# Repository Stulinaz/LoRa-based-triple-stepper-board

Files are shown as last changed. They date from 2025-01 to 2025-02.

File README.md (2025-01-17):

<!-- For .md file development refers to https://docs.github.com/en -->
# LoRa Wireless Triple Stepper Controller 

## Build for 7th PCBWAy Project Design Contest

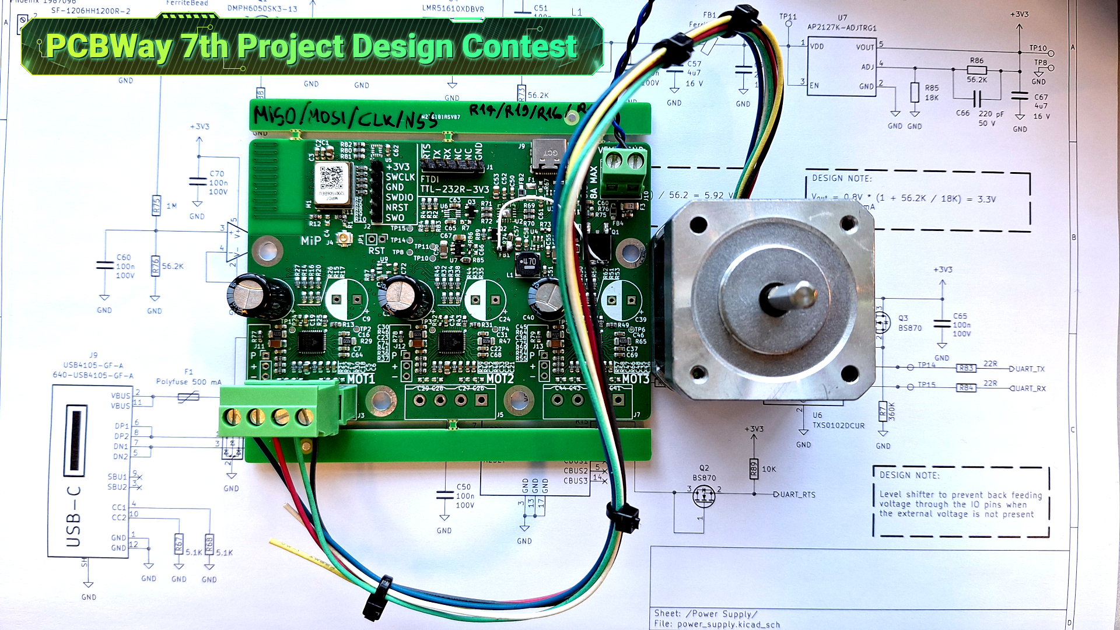
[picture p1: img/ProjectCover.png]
img_cover


[CLICK HERE](https://www.pcbway.com/project/shareproject/LoRa_based_triple_stepper_board_7cf3be2c.html) to see the project.

Designed to remote control up to three axis mechatronic system.
Build with [MIPOT](https://www.mipot.com) [32001506DEU](https://mipot.com/en/products/mip-series/dual-core/32001506deu/) LoRa Open Core module based on 
[STM32WL55JC](https://www.st.com/en/microcontrollers-microprocessors/stm32wl55cc.html) dual core microcontroller.

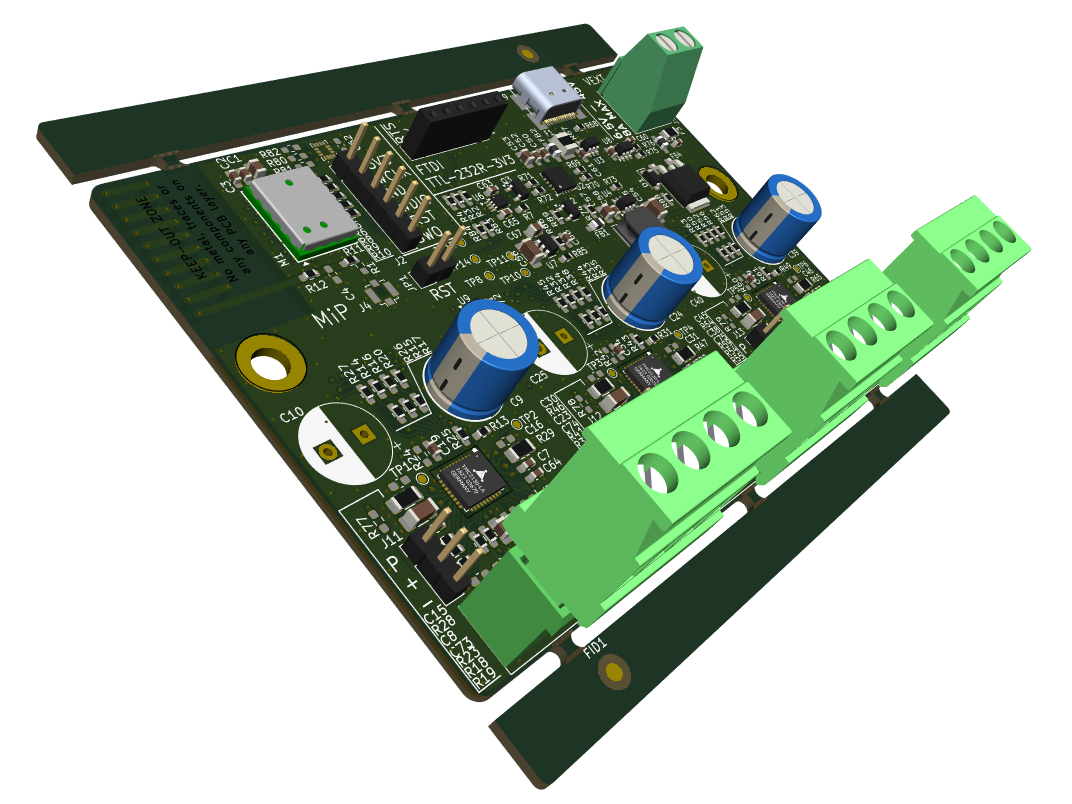
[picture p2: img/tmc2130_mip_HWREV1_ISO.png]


## Top Side of the board

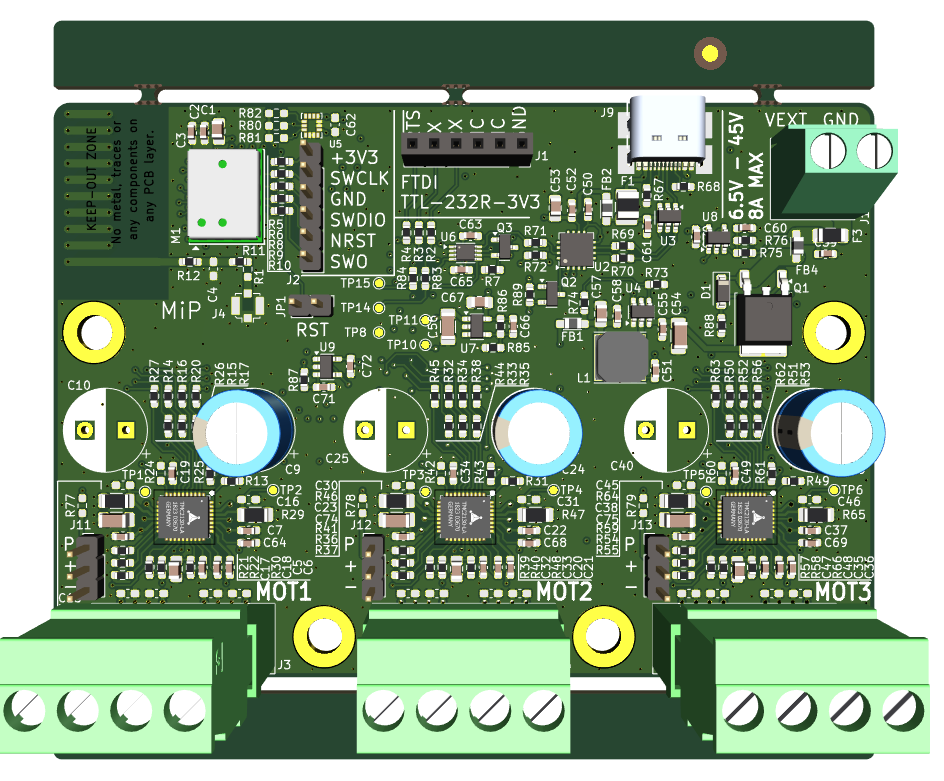
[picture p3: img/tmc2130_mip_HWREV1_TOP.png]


## Bottom Side of The board

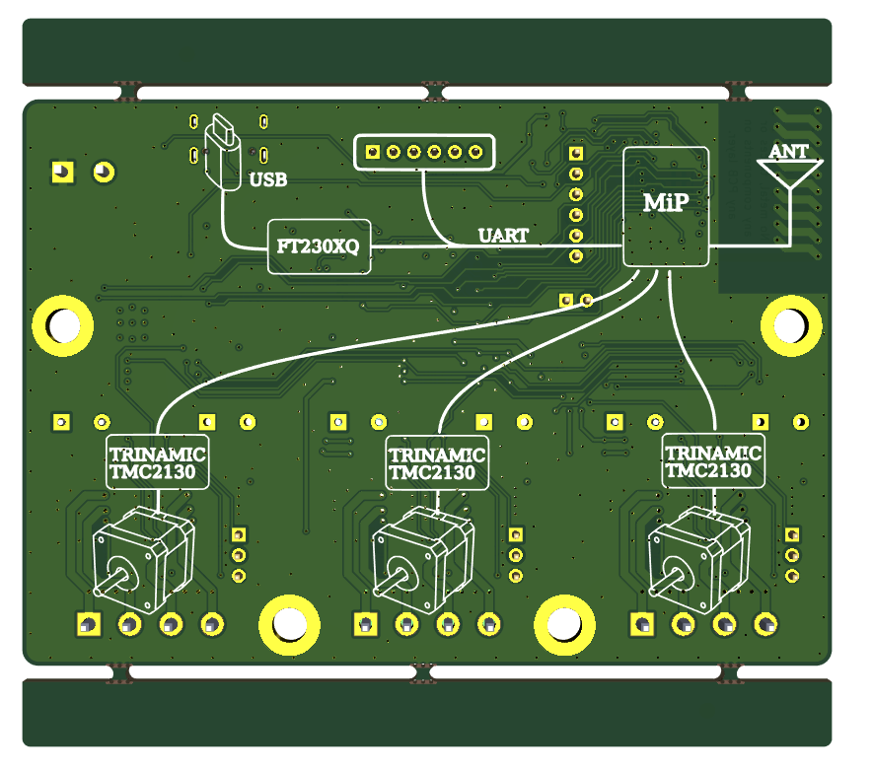
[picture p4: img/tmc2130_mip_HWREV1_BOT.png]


## Board with 4 layers for EMI Compliance

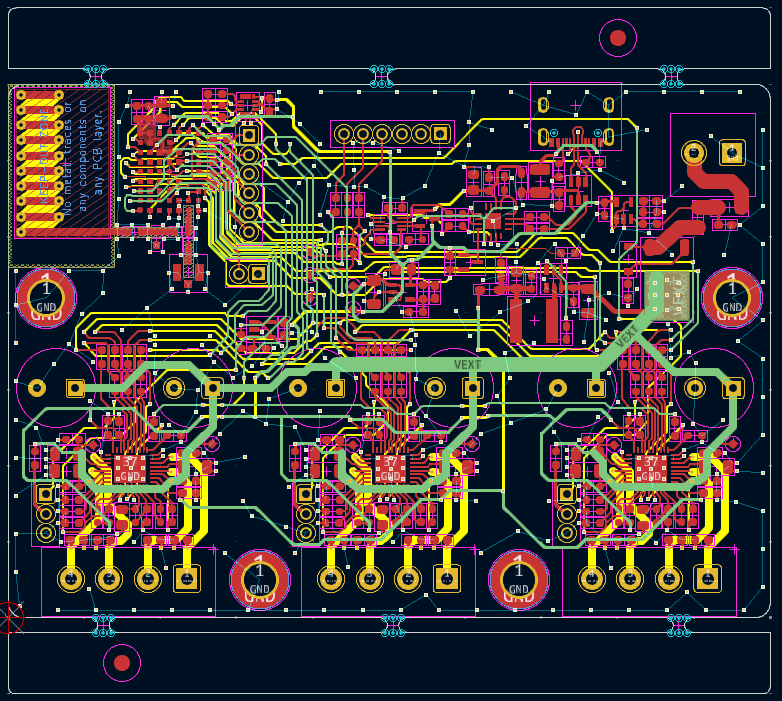
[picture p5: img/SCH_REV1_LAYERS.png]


## Build with Kicad

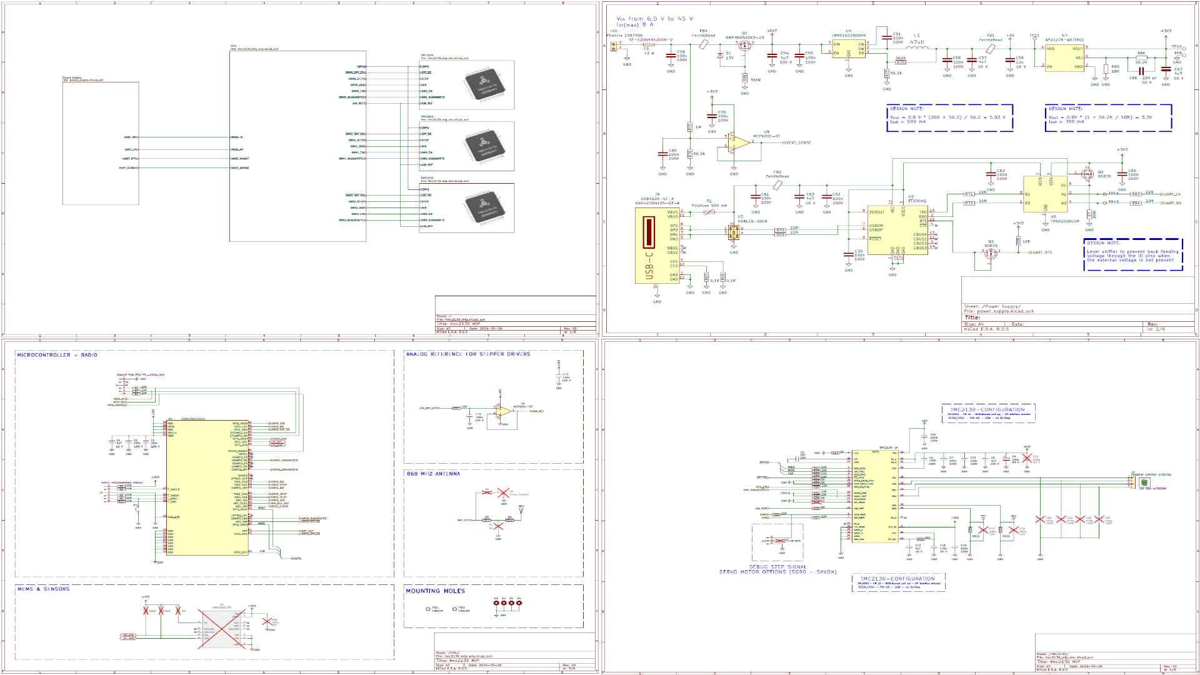
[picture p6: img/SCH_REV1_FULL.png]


## Main firwmare files for a quick view

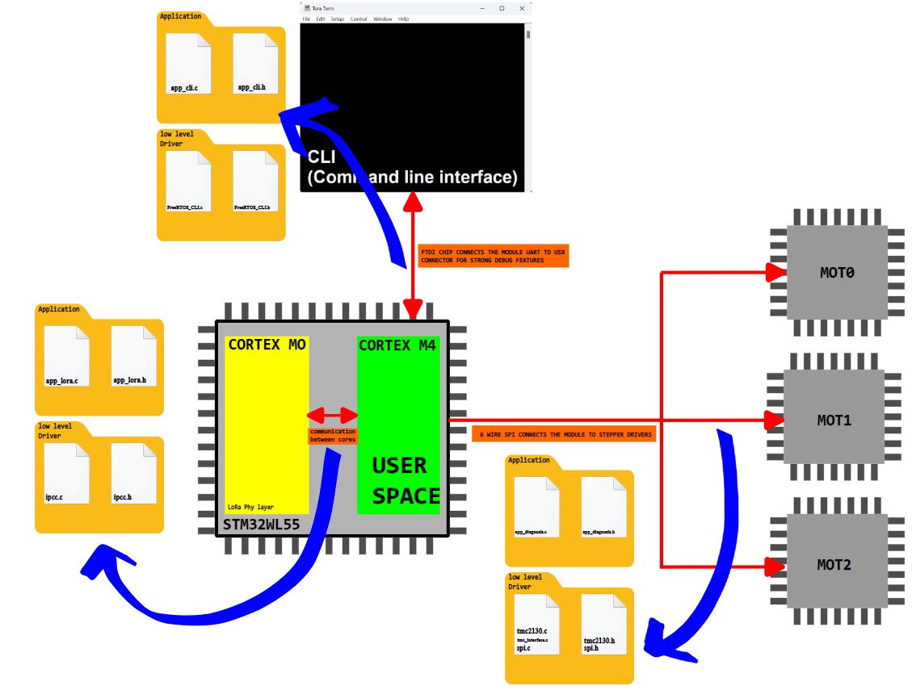
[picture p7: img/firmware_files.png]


## Pcb and stencil order on pcbway

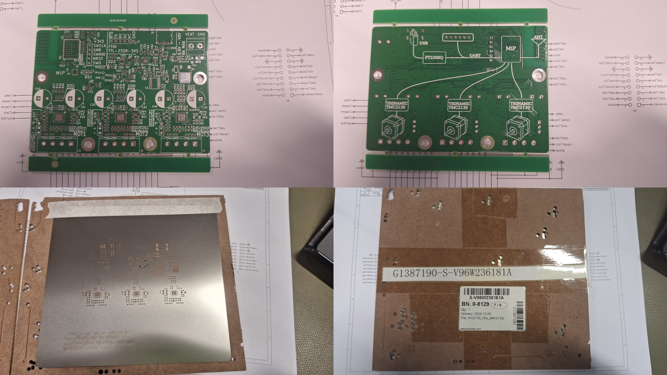
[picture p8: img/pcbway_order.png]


## Mode of Operation

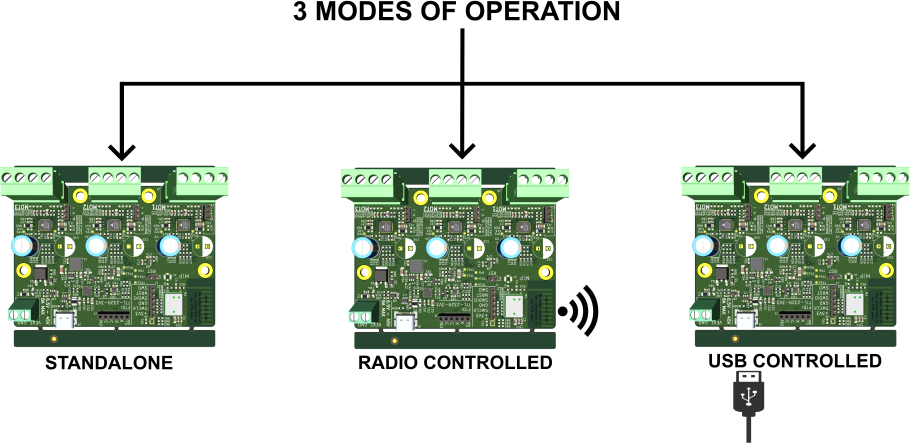
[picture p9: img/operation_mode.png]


## Closeup

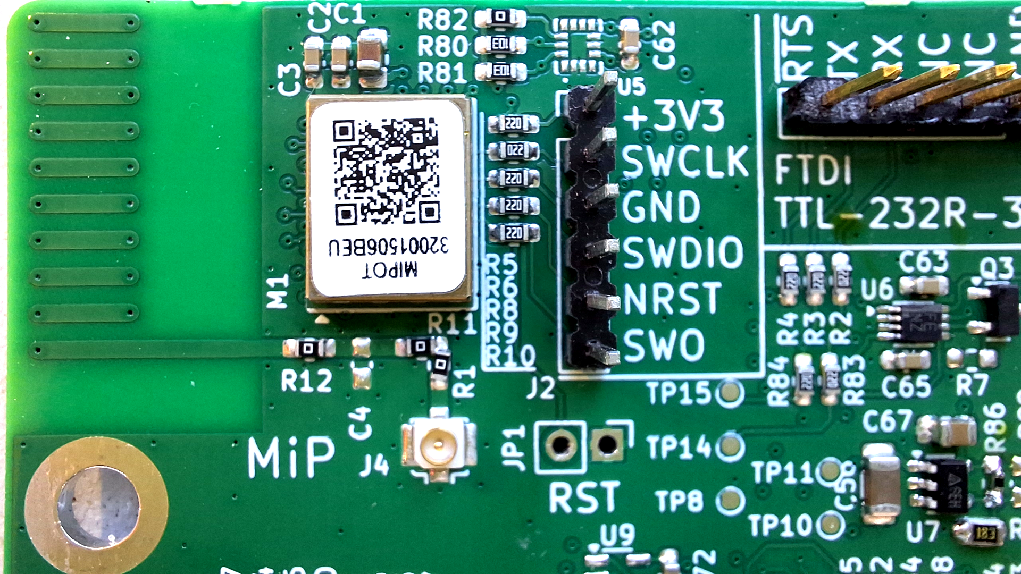
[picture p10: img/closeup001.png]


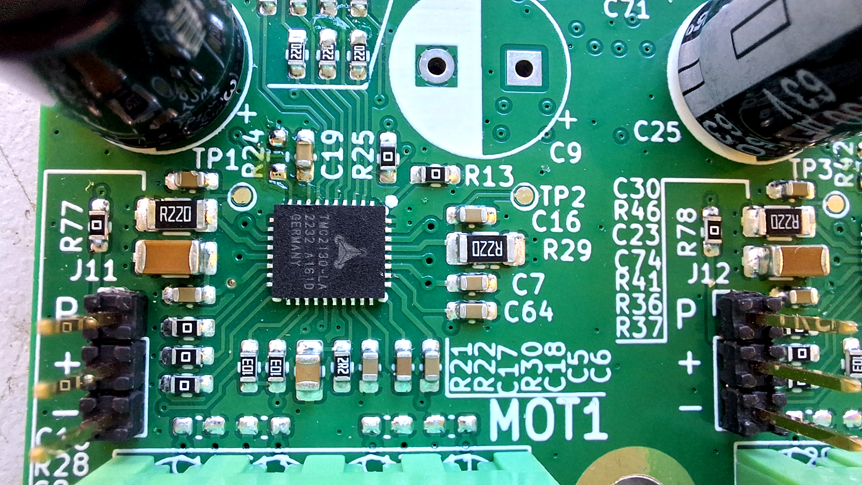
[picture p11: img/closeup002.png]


## SPI commonucation between microcontroller and TMC2130 Drivers

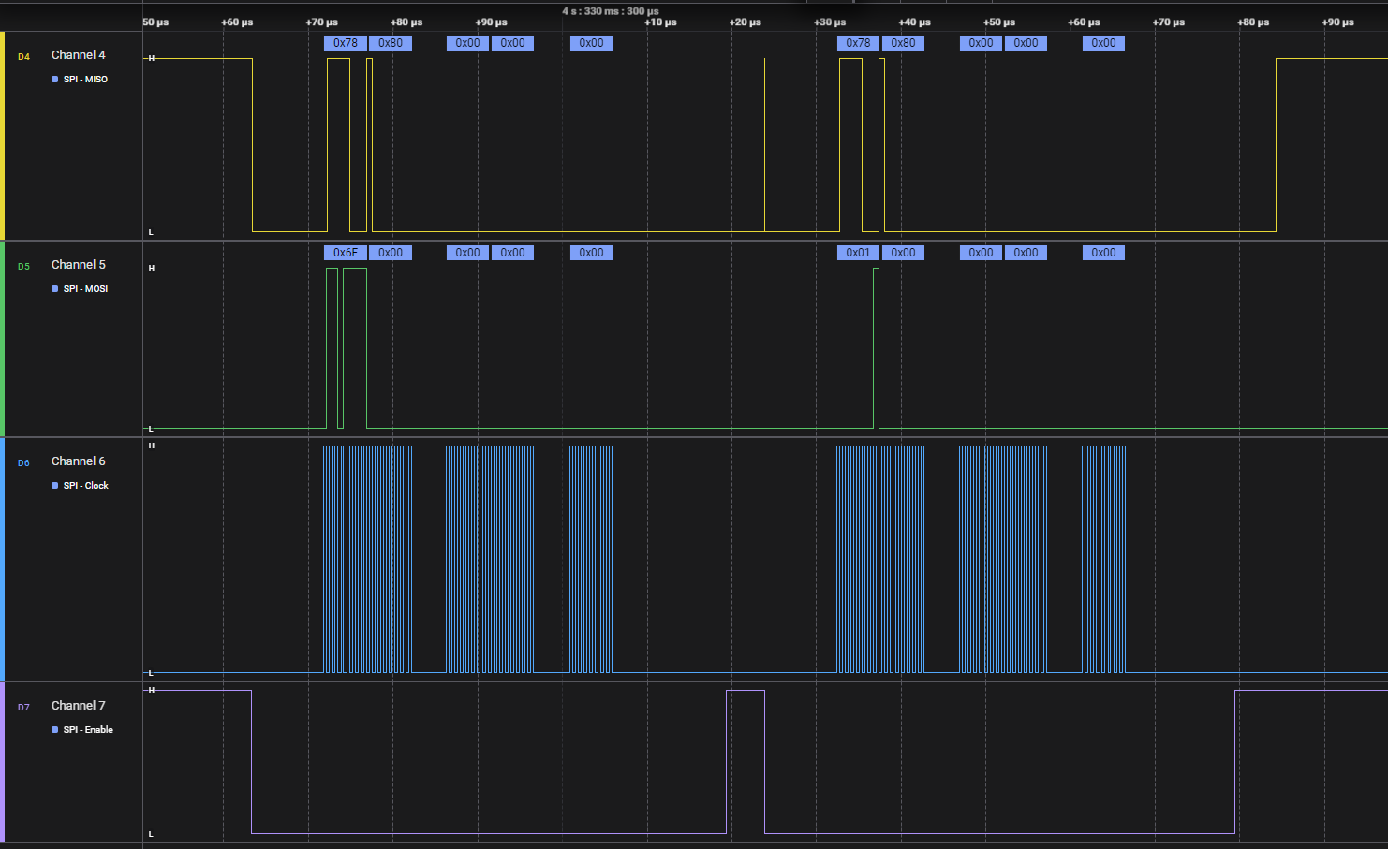
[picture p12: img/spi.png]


## Electrical characteristics

| Parameter | Description | Min | Typ | Max |  Unit  | Test Conditions | 
| --- | --- | --- | --- | --- | --- | --- |
|**Input Voltage** | - | 6 | | 45 | V | - | 
|**Operating temperature** | - | 0 | 25 | 55 | \*C | - |
|**Power consumption** | - | - | 47 | - | mA | Vcc 6Vdc - Steppers Off |

## Folder content and description

- **technical_docs:** Datasheet, Application notes and manual of the on-board electronic components.
- **firmware:** Source code of the microcontroller written in C.
	- **Core:** The application files, system and peripheral configuration.
	- **freertos:** The Freertos kernel. *Keep read only*.
	- **freertos_cli:** The Freertos command line interface source code. *Keep read only*.
	- **wl-lib:** STM32 HAL and LL Drivers. *Keep read only*.
	- **trinamic_lib:** Driver of TMC2130 stepper controller.
	- **miplib** Driver of MIPOT LoRa Module 32001506DEU. *Keep read only*.
- **img:** Development and test images of the project.
- **kicad:** hardware design files.Source files of schematic and PCB.
	- **lib:** Symbols and footprints of the components.
- **production:** Production files. Gerbers, BOM and Stencil.
- **doc:**  User manual of the board and Schematic. PDF format.

## Bll of materials

Interactive [BOM](https://github.com/Stulinaz/LoRa-based-triple-stepper-board/blob/master/production/ibom.html).

## Firmware characteristics

Based on [Freertos](https://www.freertos.org) with simple and clean development.
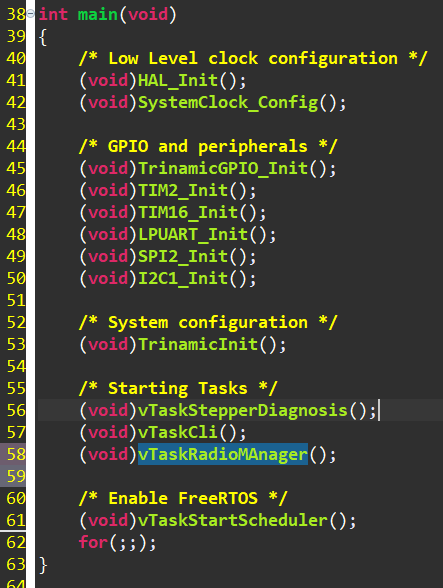
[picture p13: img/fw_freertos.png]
.

## Software needed for development

- [STM32CubeIDE](https://www.st.com/en/development-tools/stm32cubeide.html) **1.17.0**
- [KICAD](https://www.kicad.org/) **8.0.5**
- [GIT](https://git-scm.com/) **2.46.1.windows.1**
- [Tera Term](https://teratermproject.github.io/index-en.html) **5.3 x86**

## Tools needed for development

Programmer [STLINK](https://www.st.com/en/development-tools/st-link-v2.html).

## License

Shown in the LICENSE.md file

## Developers

Hardware developer: [@ts-manuel](https://github.com/ts-manuel)
Firmware developer: [@Stulinaz](https://github.com/Stulinaz)

> [!CAUTION]
> Manual soldering of SMD components requires high level of manual skills.
> Project not suited for beginners in firmware development.
> A good understanding of C language is a must.

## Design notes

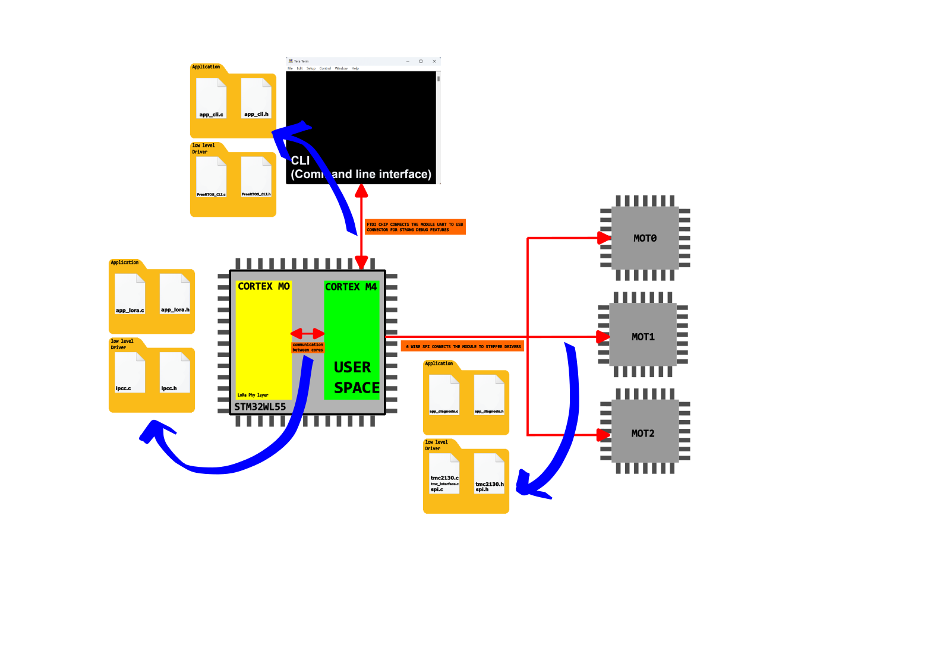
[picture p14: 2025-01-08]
img/firmware_schematic.png

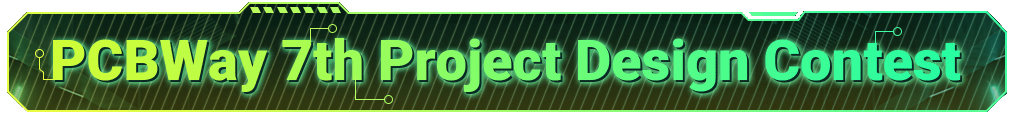
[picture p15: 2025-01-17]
img/7thProjectDesignContest.png

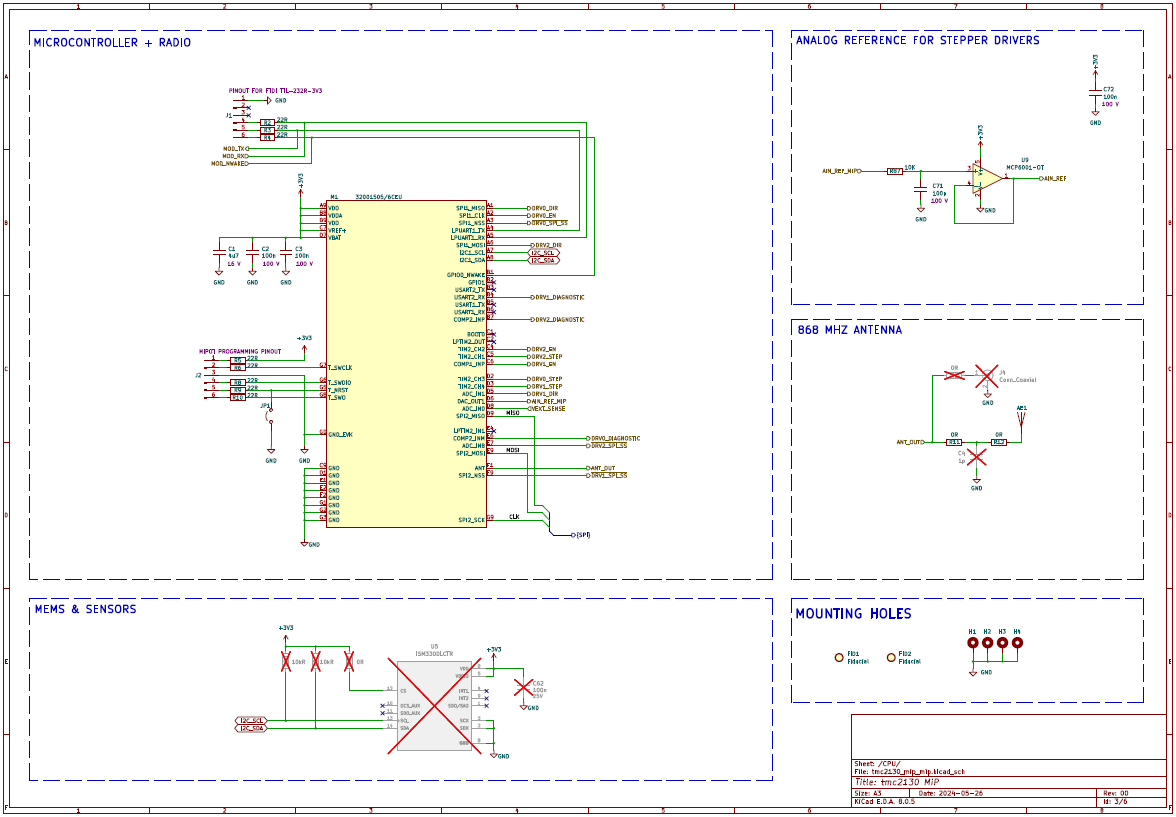
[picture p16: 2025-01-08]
img/SCH_REV1_P3.png

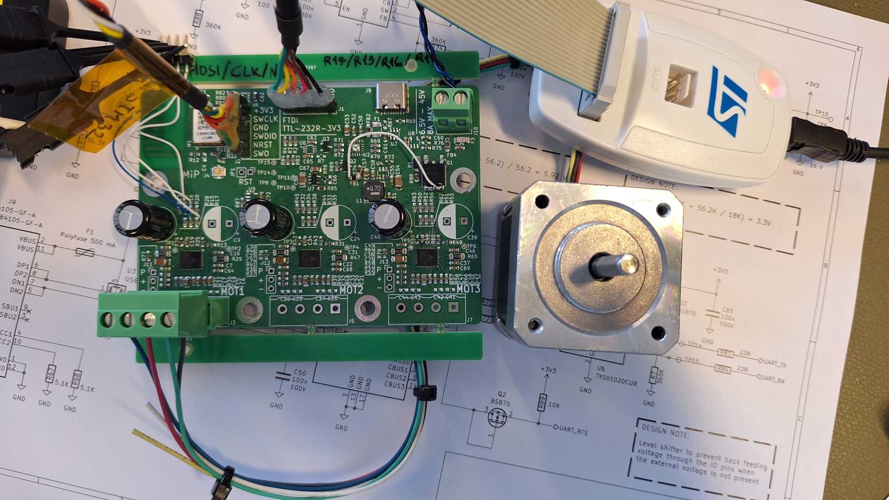
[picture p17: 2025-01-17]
img/img_develop001.png

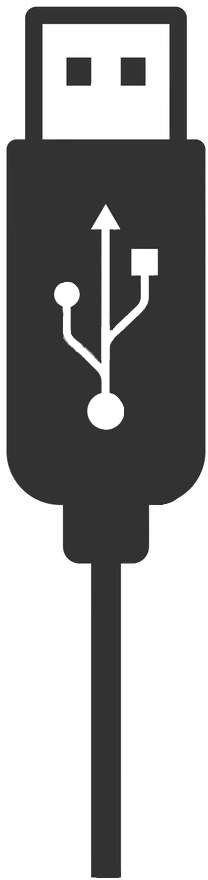
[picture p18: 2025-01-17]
img/usb_symbol.png

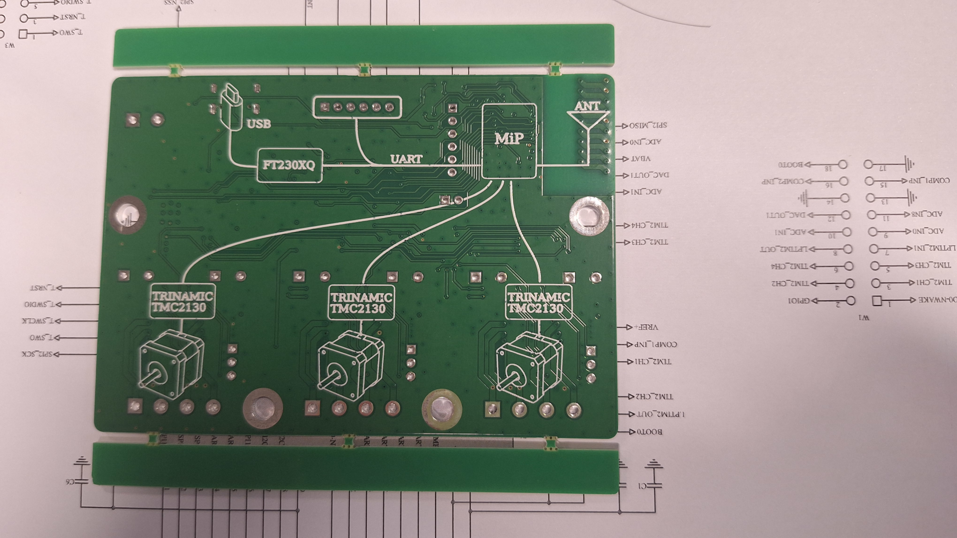
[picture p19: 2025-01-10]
img/pcb_bot.png

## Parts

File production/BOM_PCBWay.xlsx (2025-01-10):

 |  |  | LoRa based triple stepper board PCS BOM
Item # | *Designator | *Qty | Manufacturer | *Mfg Part # | Description / Value | *Package/Footprint | Type | ORDER CODE(MOUSER)
1 | C1,C17,C32,C47,C53,C57,C67 | 7 | MURATA | GRM21BR71C475KE51L | Multilayer Ceramic Capacitors MLCC - SMD/SMT 4.7 uF 16 VDC 10% 0805 X7R | C0805 | SMD | 81-GRM21BR71C475KE1L
2 | C2,C3,C6,C7,C19,C21,C22,C34,C36,C37,C49,C50,C51,C52,C55,C58,C59,C60,C61,C63,C64,C65,C68,C69,C70,C71,C72,C73,C74,C75 | 30 | SAMSUNG | CL10B104KC8NNNC | Multilayer Ceramic Capacitors MLCC - SMD/SMT 100nF+/-10% 100V X7R 0603 | C0603 | SMD | 187-CL10B104KC8NNNC
3 | C5,C20,C35 | 3 | TDK | C1608X7R1H223K080AA | Multilayer Ceramic Capacitors MLCC - SMD/SMT 0603 50VDC 22nF 10% X7R 0.8mm | C0603 | SMD | 810-C1608X7R1H223K
4 | C8,C23,C38,C54 | 4 | MURATA | GRM31CZ72A475KE11L | Multilayer Ceramic Capacitors MLCC - SMD/SMT 4.7 uF 100 VDC 10% 1206 X7R | C1206 | SMD | 81-GRM31CZ72A475K11L
5 | C9,C24,C39 | 3 | YAGEO | C0603C221J5GACAUTO7411 | Multilayer Ceramic Capacitors MLCC - SMD/SMT 50V 220pF C0G 0603 5% AEC-Q200 | C0603 | SMD | 667-EEU-FR1J151
6 | C18,C33,CC48 | 3 | SAMSUNG | CL10B474KA8NNNC | Multilayer Ceramic Capacitors MLCC - SMD/SMT 470nF+/-10% 25V X7R 0603 | C0603 | SMD | 187-CL10B474KA8NNNC
7 | C56 | 1 | KEMET | C0603C221J5GACAUTO7411 | Multilayer Ceramic Capacitors MLCC - SMD/SMT 50V 220pF C0G 0603 5% AEC-Q200 | C0603 | SMD | 80-C0603C221J5GAUTLR
8 | D1 | 1 | NEXPERIA | BZT52-C13J | Zener Diodes BZT52-C13/SOD123/SOD2 | SOD-123-2 | SMD | 771-BZT52-C13J
9 | F1 | 1 | LITTLEFUSE | MICROSMD050F-2 | Resettable Fuses - PPTC .5A 13.2V 40A Imax | 1210 | SMD | 650-MICROSMD050F-2
10 | F3 | 1 | BOURNS | SF-1206HH1200R-2 | Surface Mount Fuses 1206 high-current met-foil. 12A | 1206 | SMD | SF-1206HH1200R-2
11 | FB1,FB2,FB4 | 3 | WURTH ELEKTRONIK | 742792030 | Ferrite Beads WE-CBF 3mOhms 10K mA805 AEC-Q200 | 0805 | SMD | 710-742792030
12 | J3,J5,J7 | 3 | PHOENIX CONTACT | 1755752 | Pluggable Terminal Blocks 4 Pos 5.08mm pitch Through Hole Header | Pitch 5.08mm | THT | 651-1755752
13 | J4 | 1 | MOLEX | 73412-0110 | RF Connectors / Coaxial Connectors MCX V PCB JACK SMT 1.25MM MNT HGT |  | SMD | 538-73412-0110
14 | J9 | 1 | GCT | USB4105-GF-A | USB Connectors USB Type C,2.0, Rec,SMT, 0.95mmTH Shell Stakes,G/F,RA,Top Mnt,T&R |  | SMD | 640-USB4105-GF-A
15 | J10 | 1 | PHOENIX CONTACT | 1987096 | Fixed Terminal Blocks MKDSN 2,5/ 2-5,08 SZS-SCREW | Pitch 5.08mm | SMD | 651-1987096
16 | J15,J16,J17 | 3 | PHOENIX CONTACT | 1792265 | Pluggable Terminal Blocks 4 Pos 5.08mm pitch Plug 24-12 AWG Screw |  |  | 651-1792265
17 | L1 | 1 | TAIYO YUDEN | NRS6028T470MMGJ | Power Inductors - SMD 963-LSXND6060WHL470M RPLCMT PN 6028 47uH 390mOhms |  | SMD | 963-NRS6028T470MMGJ
18 | M1 | 1 | MIPOT | 32001505/6CEU | 32001506BEU - MIPOT DUAL CORE LoRa MODULE | LGA | SMD | https://mipot.com/en/products/mip-series/dual-core/32001506deu/
19 | MOT1,MOT2,MOT3 | 3 | ANALOG DEVICES | TMC2130-LA | Motor/Motion/Ignition Controllers & Drivers Silent stepper motor driver 5 to 46V, up to 1.2A with S/D and SPI Interface, 256 Steps, CoolStep, StallGuard and StealthChop |  | SMD | 700-TMC2130LA
20 | Q1 | 1 | DIODES INCORPORATED | DMPH6050SK3-13 | MOSFETs MOSFET BVDSS | DPAK-3 | SMD | 621-DMPH6050SK3-13
21 | Q2,Q3 | 2 | DIODES INCORPORATED | BS870-7-F | MOSFETs 60V 310mW | SOT-23-3 | SMD | 621-BS870-F
22 | R2,R3,R4,R5,R6,R8,R9,R10,R14,R15,R16,R17,R20,R26,R27,R32,R33,R34,R35,R38,R44,R45,R50,R51,R52,R53,R56,R62,R63,R69,R70,R71,R72,R83,R84 | 35 | YAGEO | AC0603JR-0722RL | Thick Film Resistors - SMD 22 Ohms 100 mW 0603 5% AEC-Q200 Standard Power Version | R0603 | SMD | 603-AC0603JR-0722RL
23 | R7,R74,R88 | 3 | YAGEO | RT0603FRE07360KL | Thick Film Resistors - SMD 360k Ohms 100 mW 0603 5% AEC-Q200 Standard Power Version | R0603 | SMD | 603-RT0603FRE07360KL
24 | R11,R12,R13,R18,R19,R23,R25,R31,R36,R37,R41,R43,R49,R54,R55,R59,R61 | 17 | YAGEO | RC0603FR-100RL | Thick Film Resistors - SMD 0 Ohms 100-200mW 0603 1% | R0603 | SMD | 603-RC0603FR-100RL
25 | R21,R22,R39,R40,R57,R58,R87,R89 | 8 | YAGEO | RC0603JR-0710KL | Thick Film Resistors - SMD 10 kOhms 100 mW 0603 5% | R0603 | SMD | 603-RC0603JR-0710KL
26 | R28,R29,R46,R47,R64,R65 | 6 | YAGEO | RL1206FR-070R22L | Current Sense Resistors - SMD 220 mOhms 250mW 1 % 600 ppm/C | R1206 | SMD | 603-RL1206FR070R22L
27 | R30,R48,R66 | 3 | YAGEO | RC0603JR-072R2L | Thick Film Resistors - SMD 2.2 Ohms 100 mW 0603 5% | R0603 | SMD | 603-RC0603JR-072R2L
28 | R67,R68 | 2 | YAGEO | RC0603FR-105K1L | Thick Film Resistors - SMD 5.1kOhms 1/10W 0603 1% | R0603 | SMD | 603-RC0603FR-105K1L
29 | R73,R76 | 2 | YAGEO | RC0402FR-0756K2L | Thick Film Resistors - SMD 56.2 kOhms 62.5mW 0402 1% | R0402 | SMD | 603-RC0402FR-0756K2L
30 | R75 | 1 | YAGEO | RC0603FR-071ML | Thick Film Resistors - SMD 1 MOhms 100mW 0603 1% | R0603 | SMD | 603-RC0603FR-071ML
31 | R85 | 1 | YAGEO | RC0402FR-0718KL | Thick Film Resistors - SMD 18 kOhms 62.5mW 0402 1% | R0402 | SMD | 603-RC0402FR-0718KL
32 | R86 | 1 | YAGEO | RC0402FR-0756K2L | Thick Film Resistors - SMD 56.2 kOhms 62.5mW 0402 1% | R0603 | SMD | 603-RC0402FR-0756K2L
33 | U2 | 1 | FTDI | FT230XQ-R | USB Interface IC USB to Basic Serial UART IC QFN-16 | QFN16 | SMD | 895-FT230XQ-R
34 | U3 | 1 | STMICROELECTRONICS | USBLC6-2SC6 | ESD Protection Diodes / TVS Diodes ESD Protection Low Cap | SOT23-6 | SMD | 511-USBLC6-2SC6
35 | U4 | 1 | TEXAS INSTRUMENTS | LMR51610XDBVR | Switching Voltage Regulators SIMPLE SWITCHER power converter with 4.5V-to-65V 1A synchronous buck and 25uA quiescent current 6-SOT-23 -40 to 150 | SOT23-6 | SMD | 595-LMR51610XDBVR
36 | U6 | 1 | TEXAS INSTRUMENTS | TXS0102DCUR | Translation - Voltage Levels 2-Bit Bi-Directional Voltage-Level-Trans | VSSOP-8 | SMD | 595-TXS0102DCUR
37 | U7 | 1 | DIODES INCORPORATED | AP2127K-ADJTRG1 | LDO Voltage Regulators 300mA CMOS LDO 2.5V to 6V | SOT23-5 | SMD | 621-AP2127K-ADJTRG1
38 | U8,U9 | 2 | MICROCHIP | MCP6001T-E/OT | Operational Amplifiers - Op Amps Single 1.8V 1MHz | SOT23-5 | SMD | 579-MCP6001T-E/OT

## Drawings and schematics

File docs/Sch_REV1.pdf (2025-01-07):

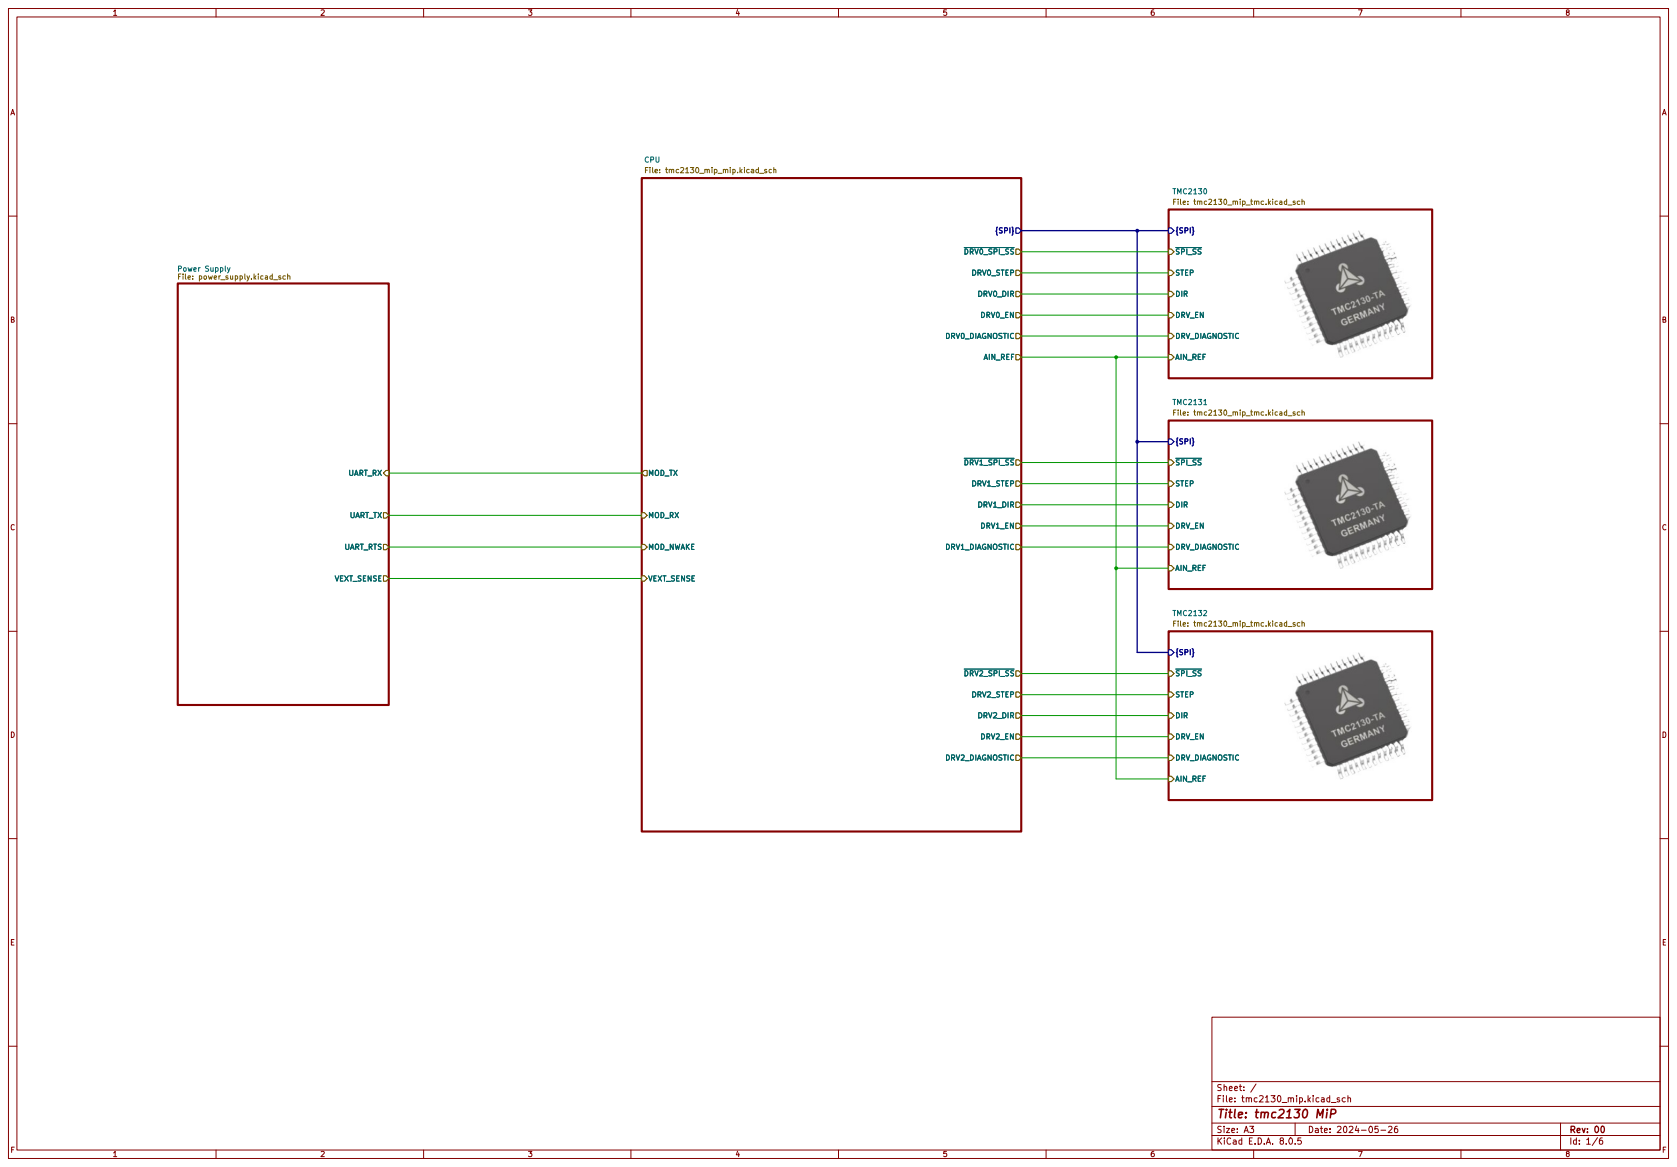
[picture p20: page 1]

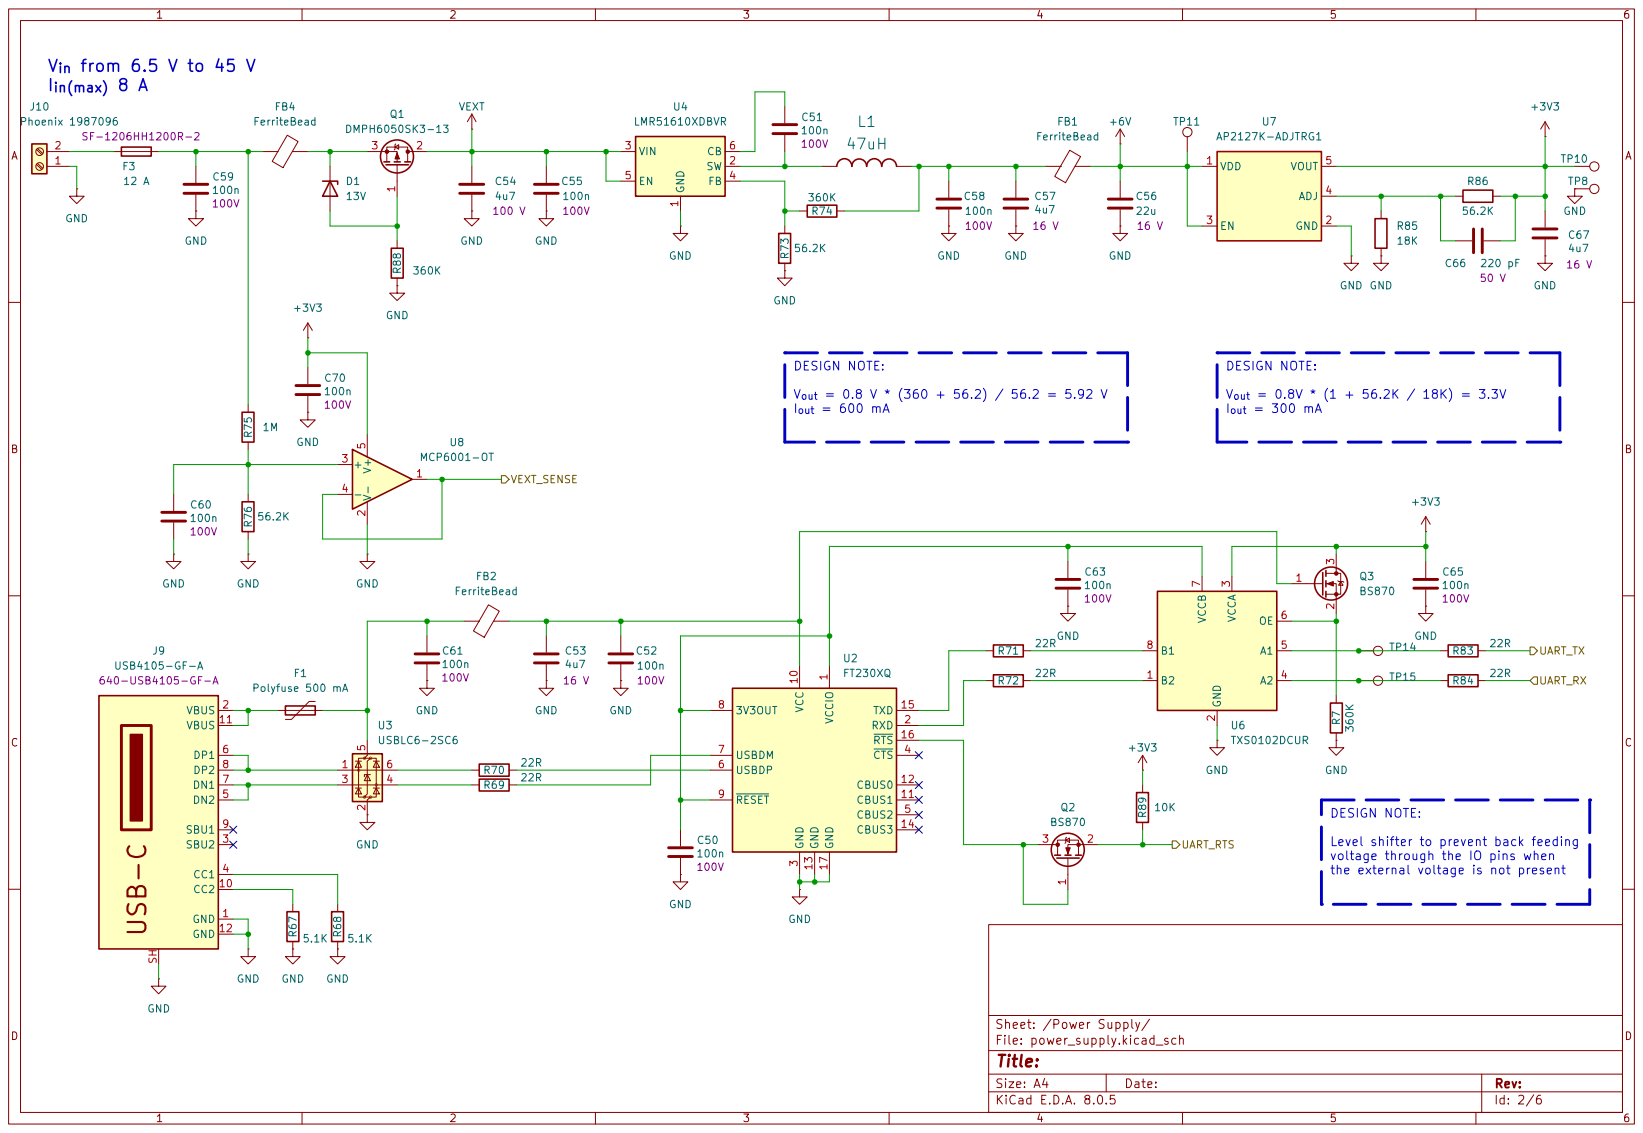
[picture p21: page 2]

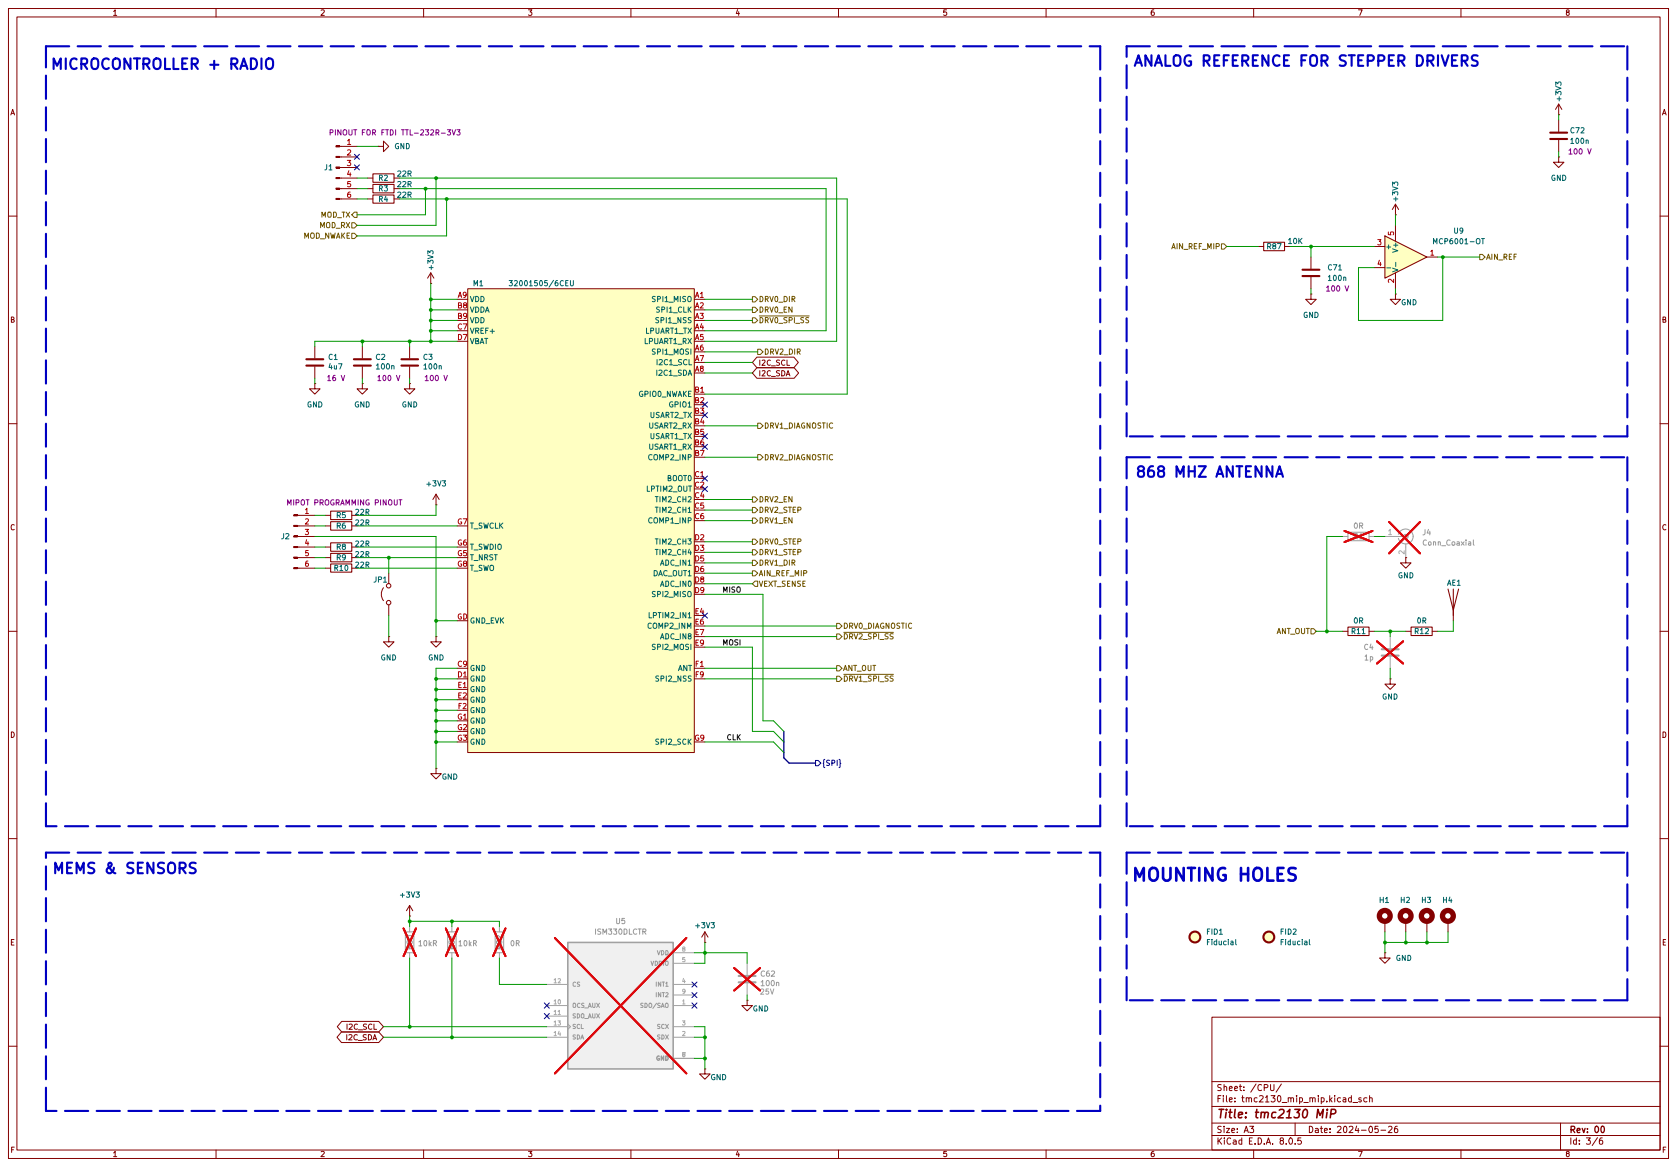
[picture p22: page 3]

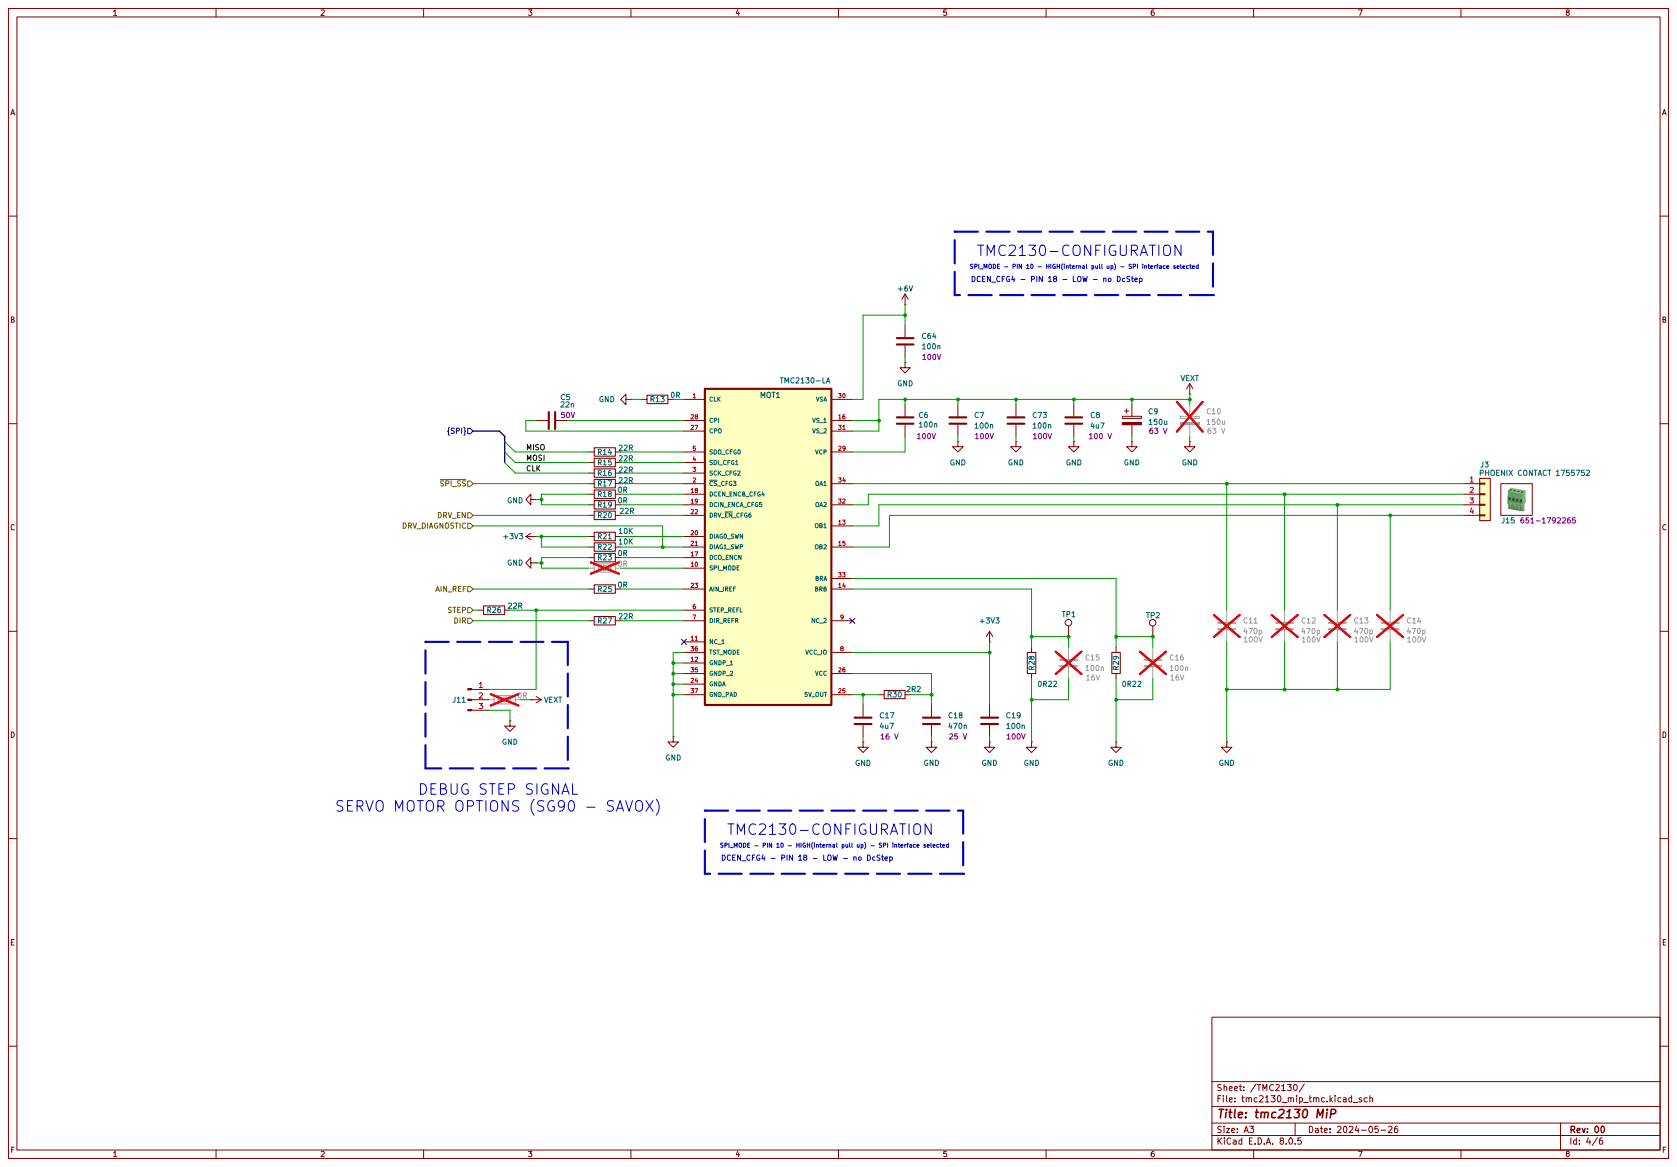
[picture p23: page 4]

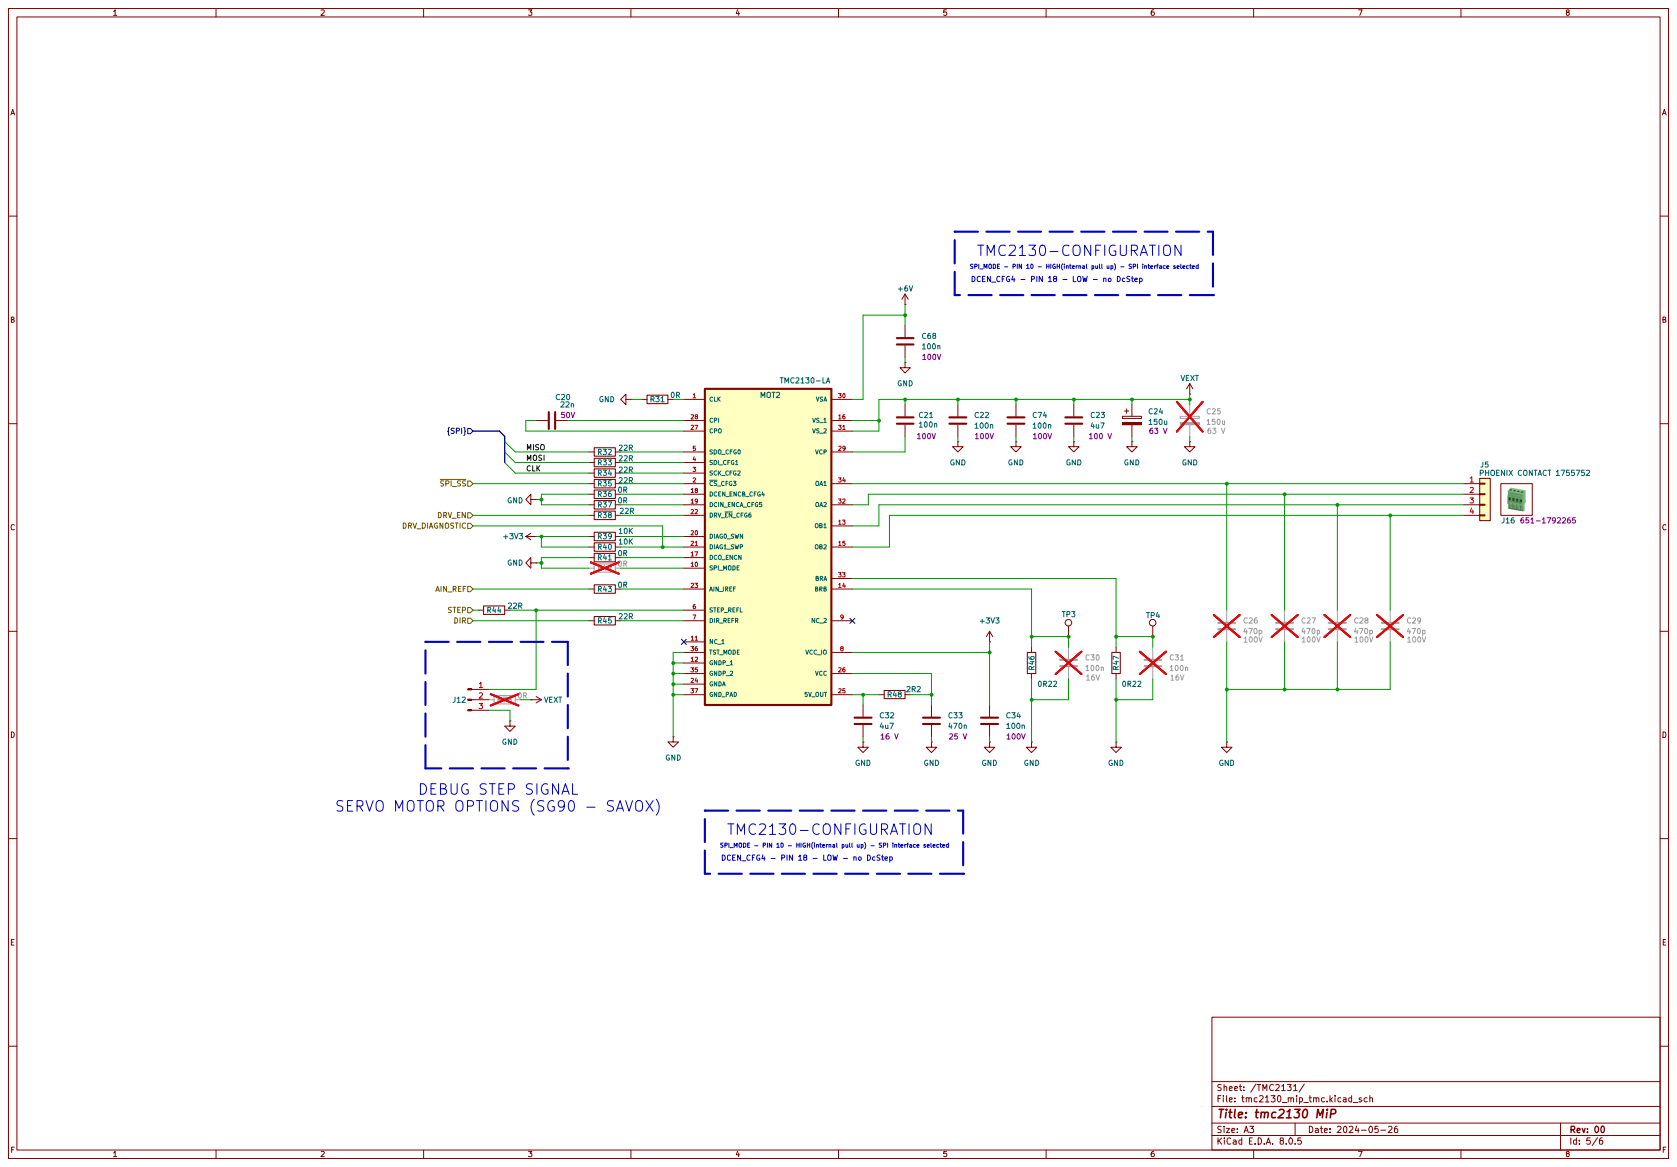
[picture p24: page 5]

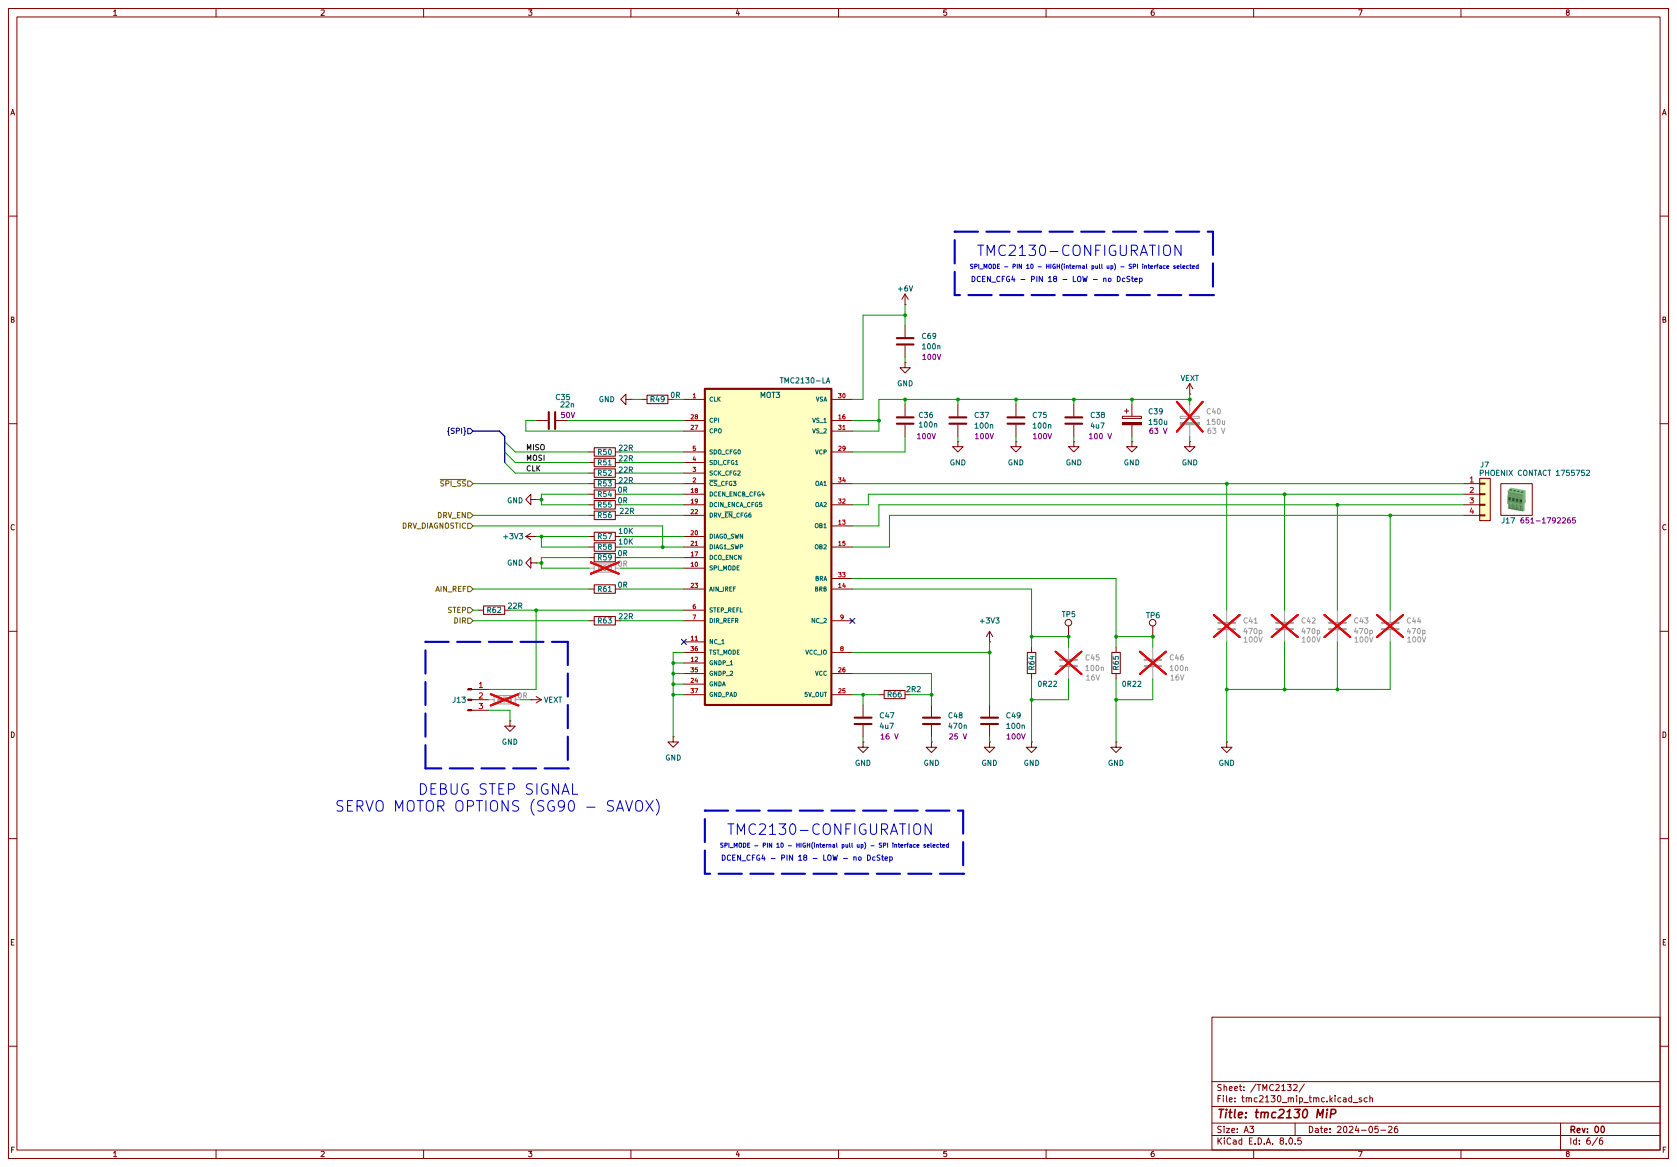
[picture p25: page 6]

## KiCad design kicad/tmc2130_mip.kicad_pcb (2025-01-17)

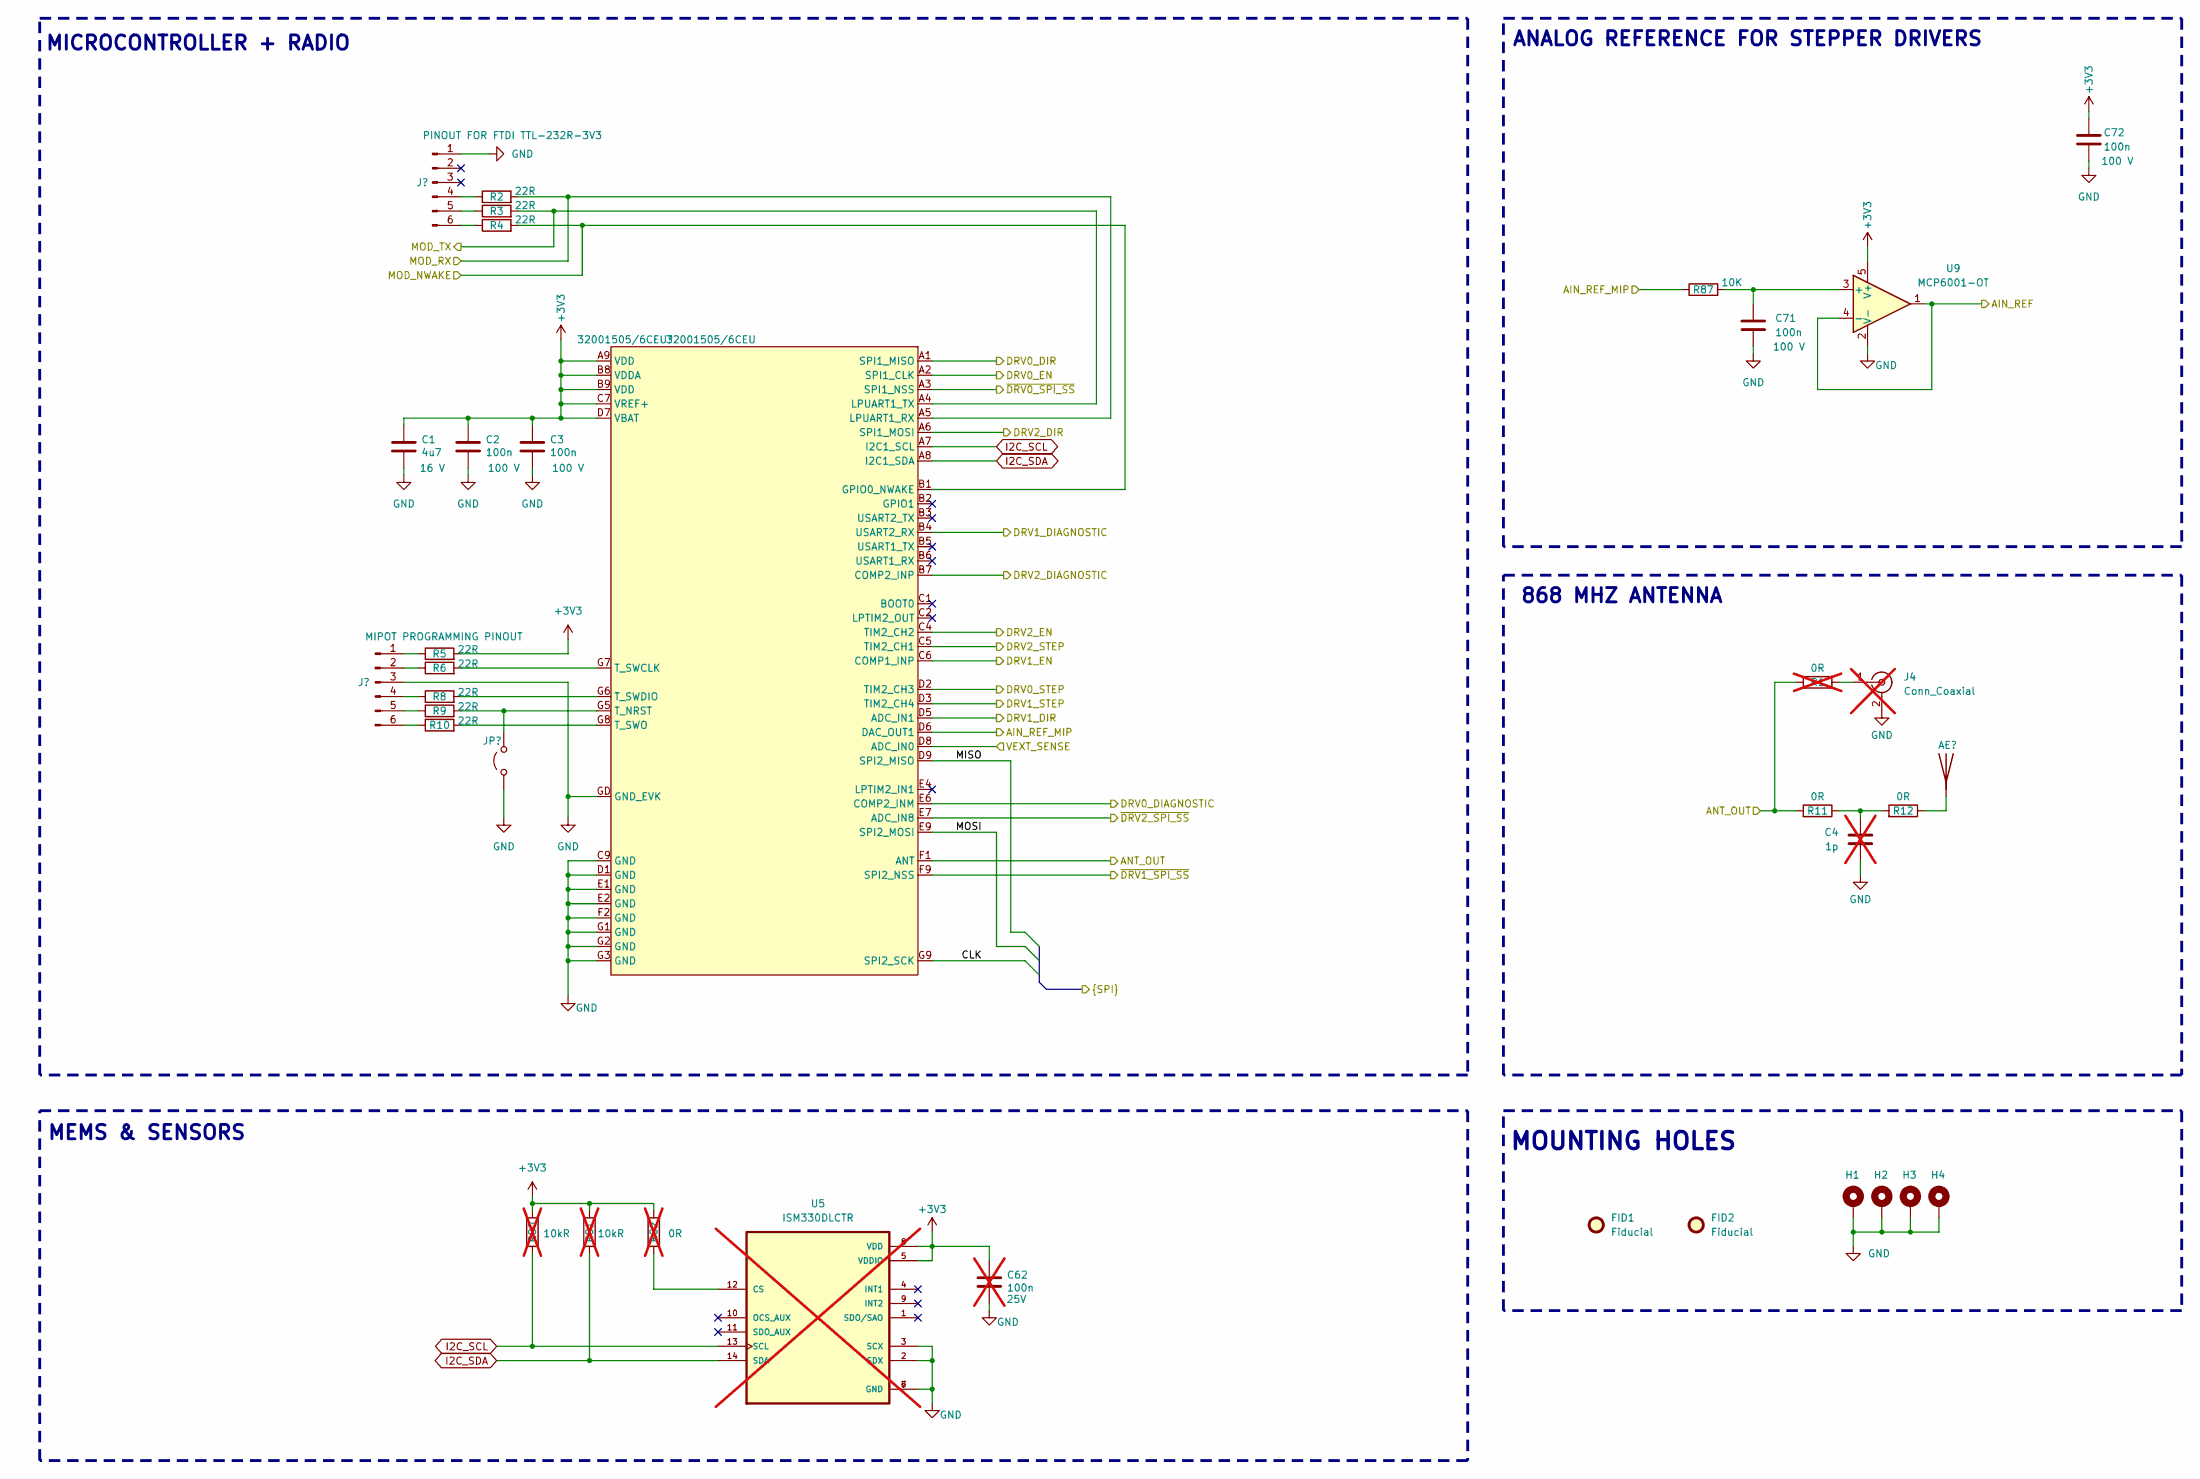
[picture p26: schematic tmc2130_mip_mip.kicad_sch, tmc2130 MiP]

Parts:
AE1: Antenna; Texas_SWRA416_868MHz_915MHz
C1: 4u7; C_0805_2012Metric_Pad1.18x1.45mm_HandSolder; Voltage 16 V; Mouser 81-GRM21BR71C475KE1L
C2, C3, C71, C72: 100n; C_0603_1608Metric_Pad1.08x0.95mm_HandSolder; Voltage 100 V; Mouser 187-CL10B104KC8NNNC
C4: 1p; C_0603_1608Metric_Pad1.08x0.95mm_HandSolder; not fitted
C62: 100n; C_0603_1608Metric_Pad1.08x0.95mm_HandSolder; not fitted
FID1, FID2: Fiducial; Fiducial_2.0mm_Mask4.0mm
H1, H2, H3, H4: MountingHole_Pad; MountingHole_4.3mm_M4_ISO7380_Pad_TopBottom
J1: Conn_01x06_Pin; PinSocket_1x06_P2.54mm_Vertical
J2: Conn_01x06_Pin; PinHeader_1x06_P2.54mm_Vertical
J4: Conn_Coaxial; U.FL_Molex_MCRF_73412-0110_Vertical; Mouser 538-73412-0110; not fitted
JP1: Jumper_2_Open; PinHeader_1x02_P2.54mm_Vertical
M1: 32001505/6CEU; 32001514_R2
R1, R82: 0R; R_0603_1608Metric_Pad0.98x0.95mm_HandSolder; not fitted
R2, R3, R4, R5, R6, R8, R9, R10: 22R; R_0603_1608Metric_Pad0.98x0.95mm_HandSolder; Mouser 603-AC0603JR-0722RL
R11, R12: 0R; R_0603_1608Metric_Pad0.98x0.95mm_HandSolder; Mouser 603-RC0603FR-100RL
R80, R81: 10kR; R_0603_1608Metric_Pad0.98x0.95mm_HandSolder; not fitted
R87: 10K; R_0603_1608Metric_Pad0.98x0.95mm_HandSolder; Mouser 603-RC0603JR-0710KL
U5: ISM330DLCTR; PQFN50P250X300X86-14N; PARTREV 2; not fitted
U9: MCP6001-OT; SOT-23-5; Mouser 579-MCP6001T-E/OT

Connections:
+3V3: C1.2, C2.2, C3.2, C62.2, C72.2, M1.A9 (VDD), M1.B8 (VDDA), M1.B9 (VDD), M1.C7 (VREF+), M1.D7 (VBAT), R5.2, R80.1, R81.1, R82.1, U5.5 (VDDIO), U5.8 (VDD), U9.5 (V+); also elsewhere on the board
/CPU/AIN_REF: U9.1, U9.4 (-); also elsewhere on the board
/CPU/AIN_REF_MIP: M1.D6 (DAC_OUT1), R87.1
/CPU/ANT_OUT: M1.F1 (ANT), R1.2, R11.2
/CPU/CLK: M1.G9 (SPI2_SCK); also elsewhere on the board
/CPU/DRV0_DIAGNOSTIC: M1.E6 (COMP2_INM); also elsewhere on the board
/CPU/DRV0_DIR: M1.A1 (SPI1_MISO); also elsewhere on the board
/CPU/DRV0_EN: M1.A2 (SPI1_CLK); also elsewhere on the board
/CPU/DRV0_STEP: M1.D2 (TIM2_CH3); also elsewhere on the board
/CPU/DRV1_DIAGNOSTIC: M1.B4 (USART2_RX); also elsewhere on the board
/CPU/DRV1_DIR: M1.D5 (ADC_IN1); also elsewhere on the board
/CPU/DRV1_EN: M1.C6 (COMP1_INP); also elsewhere on the board
/CPU/DRV1_STEP: M1.D3 (TIM2_CH4); also elsewhere on the board
/CPU/DRV2_DIAGNOSTIC: M1.B7 (COMP2_INP); also elsewhere on the board
/CPU/DRV2_DIR: M1.A6 (SPI1_MOSI); also elsewhere on the board
/CPU/DRV2_EN: M1.C4 (TIM2_CH2); also elsewhere on the board
/CPU/DRV2_STEP: M1.C5 (TIM2_CH1); also elsewhere on the board
/CPU/MISO: M1.D9 (SPI2_MISO); also elsewhere on the board
/CPU/MOD_NWAKE: M1.B1 (GPIO0_NWAKE), R4.2; also elsewhere on the board
/CPU/MOD_RX: M1.A5 (LPUART1_RX), R2.2; also elsewhere on the board
/CPU/MOD_TX: M1.A4 (LPUART1_TX), R3.2; also elsewhere on the board
/CPU/MOSI: M1.E9 (SPI2_MOSI); also elsewhere on the board
/CPU/VEXT_SENSE: M1.D8 (ADC_IN0); also elsewhere on the board
/CPU/~DRV0_SPI_SS: M1.A3 (SPI1_NSS); also elsewhere on the board
/CPU/~DRV1_SPI_SS: M1.F9 (SPI2_NSS); also elsewhere on the board
/CPU/~DRV2_SPI_SS: M1.E7 (ADC_IN8); also elsewhere on the board
GND: C1.1, C2.1, C3.1, C4.1, C62.1, C71.1, C72.1, H1.1, H2.1, H3.1, H4.1, J1.1, J2.3, J4.2 (Ext), JP1.1 (A), M1.C9 (GND), M1.D1 (GND), M1.E1 (GND), M1.E2 (GND), M1.F2 (GND), M1.G1 (GND), M1.G2 (GND), M1.G3 (GND), M1.GD (GND_EVK), U5.2 (SDX), U5.3 (SCX), U5.6 (GND), U5.7 (GND), U9.2 (V-); also elsewhere on the board
I2C_SCL: M1.A7 (I2C1_SCL), R80.2, U5.13 (SCL)
I2C_SDA: M1.A8 (I2C1_SDA), R81.2, U5.14 (SDA)
unnamed: AE1.1 (A), R12.1
unnamed: C4.2, R11.1, R12.2
unnamed: J1.4, R2.1
unnamed: J1.5, R3.1
unnamed: J1.6, R4.1
unnamed: J2.1, R5.1
unnamed: J2.2, R6.1
unnamed: J2.4, R8.1
unnamed: J2.5, R9.1
unnamed: J2.6, R10.1
unnamed: J4.1 (In), R1.1
unnamed: JP1.2 (B), M1.G5 (T_NRST), R9.2
unnamed: M1.G7 (T_SWCLK), R6.2
unnamed: M1.G6 (T_SWDIO), R8.2
unnamed: M1.G8 (T_SWO), R10.2
unnamed: R82.2, U5.12 (CS)
unnamed: C71.2, R87.2, U9.3 (+)

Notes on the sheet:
MEMS & SENSORS
MICROCONTROLLER + RADIO
MOUNTING HOLES
ANALOG REFERENCE FOR STEPPER DRIVERS
868 MHZ ANTENNA

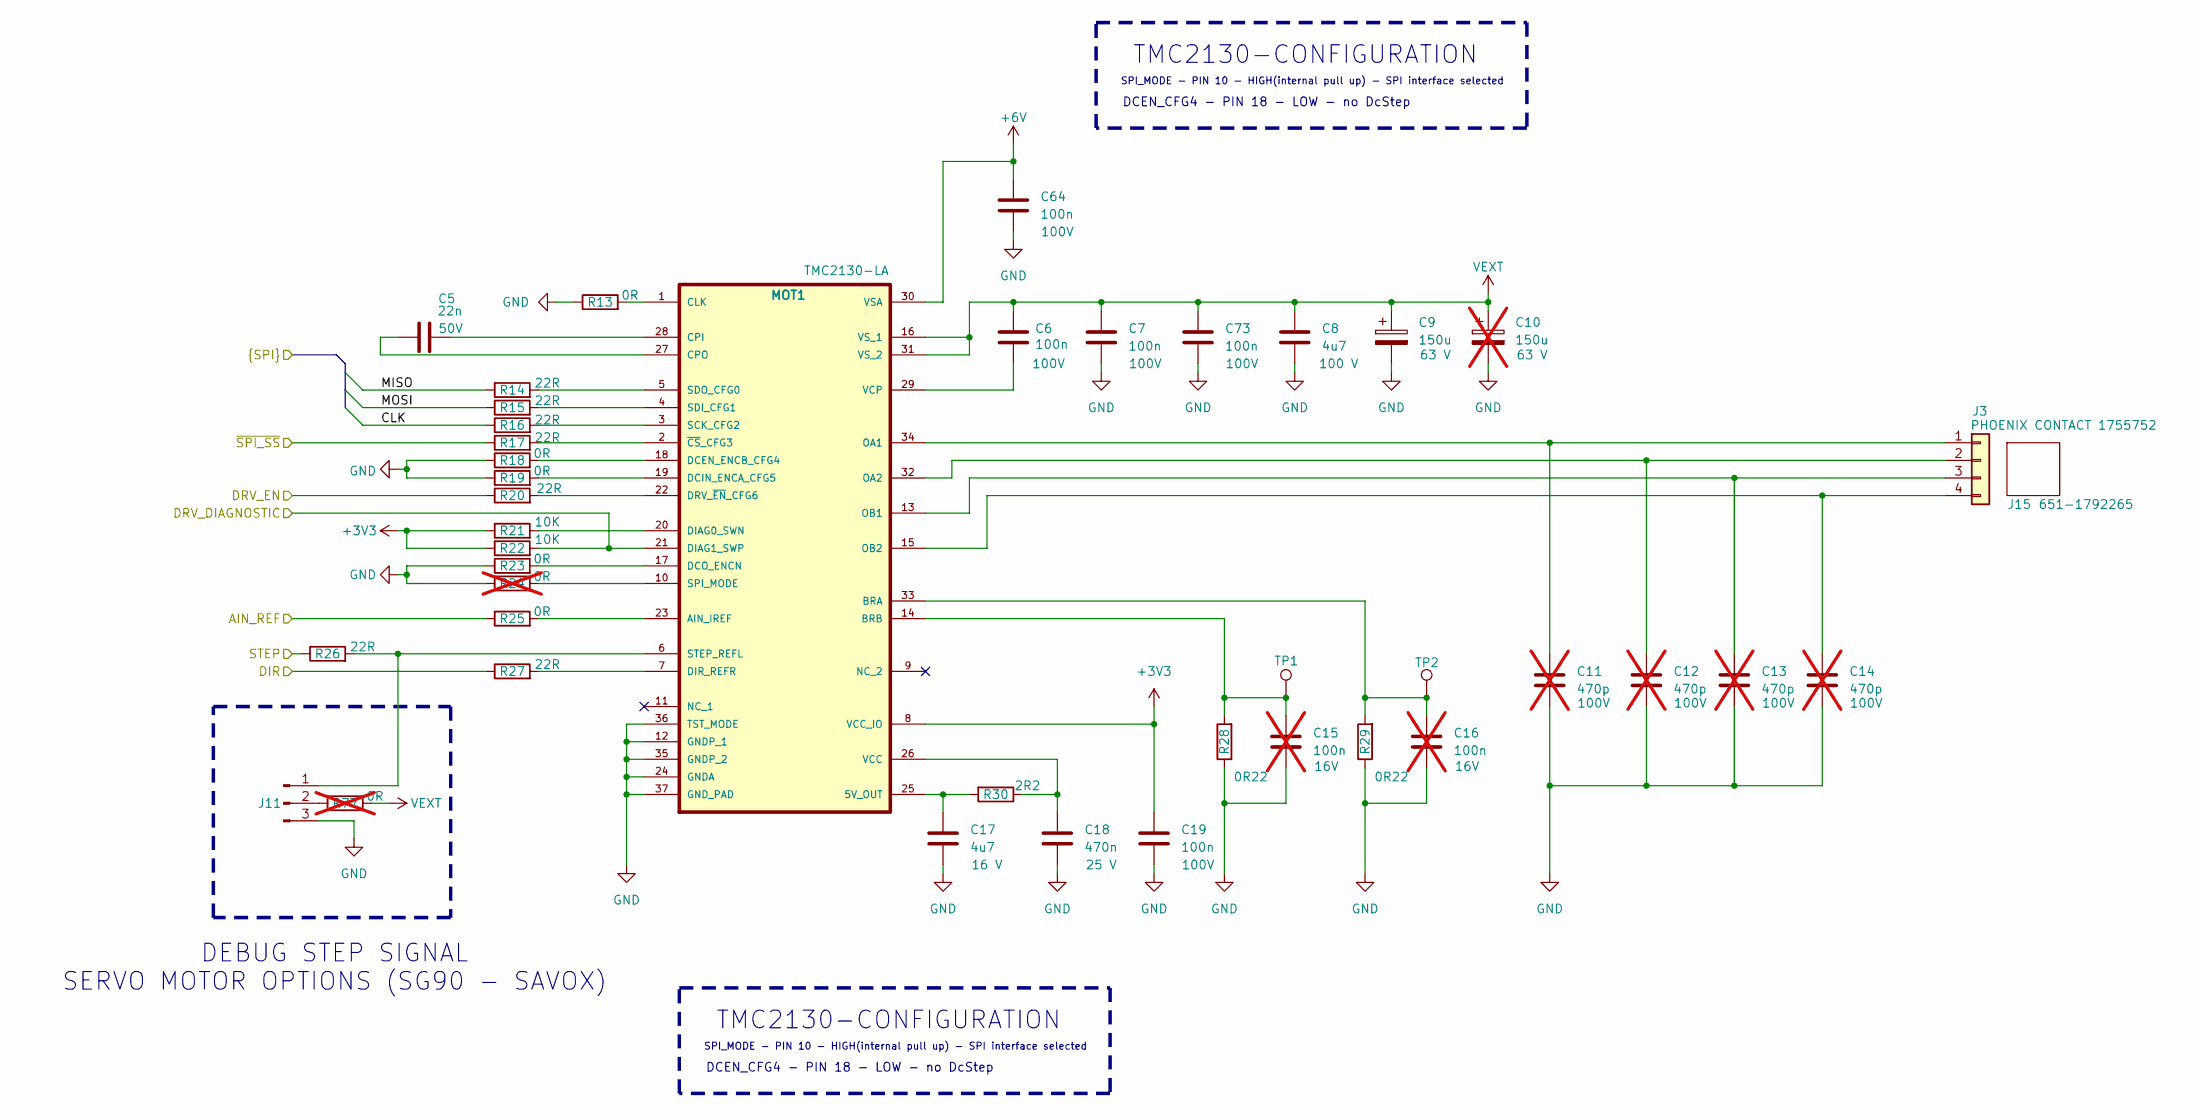
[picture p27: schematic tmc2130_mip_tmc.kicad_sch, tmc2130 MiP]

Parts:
C5: 22n; C_0603_1608Metric_Pad1.08x0.95mm_HandSolder; Voltage 50V; Mouser 810-C1608X7R1H223K
C6, C7, C19, C64, C73: 100n; C_0603_1608Metric_Pad1.08x0.95mm_HandSolder; Voltage 100V; Mouser 187-CL10B104KC8NNNC
C8: 4u7; C_1206_3216Metric_Pad1.33x1.80mm_HandSolder; Voltage 100 V; Mouser 81-GRM31CZ72A475K11L
C9: 150u; CP_Radial_D10.0mm_P5.00mm; Voltage 63 V; Mouser 667-EEU-FR1J151
C10: 150u; CP_Radial_D10.0mm_P5.00mm; Voltage 63 V; Mouser 667-EEU-FR1J151; not fitted
C11, C12, C13, C14: 470p; C_0603_1608Metric_Pad1.08x0.95mm_HandSolder; not fitted
C15, C16: 100n; C_0603_1608Metric_Pad1.08x0.95mm_HandSolder; Voltage 100 V; Mouser 187-CL10B104KC8NNNC; not fitted
C17: 4u7; C_0805_2012Metric_Pad1.18x1.45mm_HandSolder; Voltage 16 V; Mouser 81-GRM21BR71C475KE1L
C18: 470n; C_0603_1608Metric_Pad1.08x0.95mm_HandSolder; Voltage 25 V; Mouser 187-CL10B474KA8NNNC
J3: PHOENIX CONTACT 1755752; PHOENIX_1755752; Mouser 651-1755752
J11: Conn_01x03_Pin; PinHeader_1x03_P2.54mm_Vertical
J15: PHOENIX_MVSTBR 2,5 4-ST-5,08; Mouser 651-1792265
MOT1: TMC2130-LA; TMC_QFN36_0.5_5.0X6.0; Mouser 700-TMC2130LA
R13, R18, R19, R23, R25: 0R; R_0603_1608Metric_Pad0.98x0.95mm_HandSolder; Mouser 603-RC0603FR-100RL
R14, R15, R16, R17, R20, R26, R27: 22R; R_0603_1608Metric_Pad0.98x0.95mm_HandSolder; Mouser 603-AC0603JR-0722RL
R21, R22: 10K; R_0603_1608Metric_Pad0.98x0.95mm_HandSolder; Mouser 603-RC0603JR-0710KL
R24, R77: 0R; R_0603_1608Metric_Pad0.98x0.95mm_HandSolder; not fitted
R28, R29: 0R22; R_1206_3216Metric_Pad1.30x1.75mm_HandSolder; Mouser 603-RL1206FR070R22L
R30: 2R2; R_0603_1608Metric_Pad0.98x0.95mm_HandSolder; Mouser 603-RC0603JR-072R2L
TP1, TP2: TestPoint; TestPoint_Pad_D1.0mm

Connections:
+3V3: C19.2, MOT1.8 (VCC_IO), R21.1, R22.1; also elsewhere on the board
+6V: C64.2, MOT1.30 (VSA); also elsewhere on the board
/CPU/AIN_REF: R25.1; also elsewhere on the board
/CPU/CLK: R16.1; also elsewhere on the board
/CPU/DRV0_DIAGNOSTIC: MOT1.21 (DIAG1_SWP), R22.2; also elsewhere on the board
/CPU/DRV0_DIR: R27.1; also elsewhere on the board
/CPU/DRV0_EN: R20.1; also elsewhere on the board
/CPU/DRV0_STEP: R26.1; also elsewhere on the board
/CPU/MISO: R14.1; also elsewhere on the board
/CPU/MOSI: R15.1; also elsewhere on the board
/CPU/~DRV0_SPI_SS: R17.1; also elsewhere on the board
GND: C7.1, C8.1, C9.2, C10.2, C11.2, C12.2, C13.2, C14.2, C15.1, C16.1, C17.1, C18.1, C19.1, C64.1, C73.1, J11.3, MOT1.12 (GNDP_1), MOT1.24 (GNDA), MOT1.35 (GNDP_2), MOT1.36 (TST_MODE), MOT1.37 (GND_PAD), R13.1, R18.1, R19.1, R23.1, R24.1, R28.1, R29.1; also elsewhere on the board
unnamed: C11.1, J3.1, MOT1.34 (OA1)
unnamed: C12.1, J3.2, MOT1.32 (OA2)
unnamed: C13.1, J3.3, MOT1.13 (OB1)
unnamed: C14.1, J3.4, MOT1.15 (OB2)
unnamed: J11.1, MOT1.6 (STEP_REFL), R26.2
unnamed: J11.2, R77.1
unnamed: C17.2, MOT1.25 (5V_OUT), R30.2
unnamed: MOT1.23 (AIN_IREF), R25.2
unnamed: C16.2, MOT1.33 (BRA), R29.2, TP2.1
unnamed: C15.2, MOT1.14 (BRB), R28.2, TP1.1
unnamed: MOT1.1 (CLK), R13.2
unnamed: C5.1, MOT1.28 (CPI)
unnamed: C5.2, MOT1.27 (CPO)
unnamed: MOT1.18 (DCEN_ENCB_CFG4), R18.2
unnamed: MOT1.19 (DCIN_ENCA_CFG5), R19.2
unnamed: MOT1.17 (DCO_ENCN), R23.2
unnamed: MOT1.20 (DIAG0_SWN), R21.2
unnamed: MOT1.7 (DIR_REFR), R27.2
unnamed: MOT1.22 (DRV_~EN_CFG6), R20.2
unnamed: MOT1.3 (SCK_CFG2), R16.2
unnamed: MOT1.4 (SDI_CFG1), R15.2
unnamed: MOT1.5 (SDO_CFG0), R14.2
unnamed: MOT1.10 (SPI_MODE), R24.2
unnamed: C18.2, MOT1.26 (VCC), R30.1
unnamed: C6.1, MOT1.29 (VCP)
unnamed: MOT1.2 (~CS_CFG3), R17.2
VEXT: C6.2, C7.2, C8.2, C9.1, C10.1, C73.2, MOT1.16 (VS_1), MOT1.31 (VS_2), R77.2; also elsewhere on the board

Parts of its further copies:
C20, C35: 22n; C_0603_1608Metric_Pad1.08x0.95mm_HandSolder; Voltage 50V; Mouser 810-C1608X7R1H223K
C21, C22, C34, C36, C37, C49, C68, C69, C74, C75: 100n; C_0603_1608Metric_Pad1.08x0.95mm_HandSolder; Voltage 100V; Mouser 187-CL10B104KC8NNNC
C23, C38: 4u7; C_1206_3216Metric_Pad1.33x1.80mm_HandSolder; Voltage 100 V; Mouser 81-GRM31CZ72A475K11L
C24, C39: 150u; CP_Radial_D10.0mm_P5.00mm; Voltage 63 V; Mouser 667-EEU-FR1J151
C25, C40: 150u; CP_Radial_D10.0mm_P5.00mm; Voltage 63 V; Mouser 667-EEU-FR1J151; not fitted
C26, C27, C28, C29, C41, C42, C43, C44: 470p; C_0603_1608Metric_Pad1.08x0.95mm_HandSolder; not fitted
C30, C31, C45, C46: 100n; C_0603_1608Metric_Pad1.08x0.95mm_HandSolder; Voltage 100 V; Mouser 187-CL10B104KC8NNNC; not fitted
C32, C47: 4u7; C_0805_2012Metric_Pad1.18x1.45mm_HandSolder; Voltage 16 V; Mouser 81-GRM21BR71C475KE1L
C33, C48: 470n; C_0603_1608Metric_Pad1.08x0.95mm_HandSolder; Voltage 25 V; Mouser 187-CL10B474KA8NNNC
J5, J7: PHOENIX CONTACT 1755752; PHOENIX_1755752; Mouser 651-1755752
J12, J13: Conn_01x03_Pin; PinHeader_1x03_P2.54mm_Vertical
J16, J17: PHOENIX_MVSTBR 2,5 4-ST-5,08; Mouser 651-1792265
MOT2, MOT3: TMC2130-LA; TMC_QFN36_0.5_5.0X6.0; Mouser 700-TMC2130LA
R31, R36, R37, R41, R43, R49, R54, R55, R59, R61: 0R; R_0603_1608Metric_Pad0.98x0.95mm_HandSolder; Mouser 603-RC0603FR-100RL
R32, R33, R34, R35, R38, R44, R45, R50, R51, R52, R53, R56, R62, R63: 22R; R_0603_1608Metric_Pad0.98x0.95mm_HandSolder; Mouser 603-AC0603JR-0722RL
R39, R40, R57, R58: 10K; R_0603_1608Metric_Pad0.98x0.95mm_HandSolder; Mouser 603-RC0603JR-0710KL
R42, R60, R78, R79: 0R; R_0603_1608Metric_Pad0.98x0.95mm_HandSolder; not fitted
R46, R47, R64, R65: 0R22; R_1206_3216Metric_Pad1.30x1.75mm_HandSolder; Mouser 603-RL1206FR070R22L
R48, R66: 2R2; R_0603_1608Metric_Pad0.98x0.95mm_HandSolder; Mouser 603-RC0603JR-072R2L
TP3, TP4, TP5, TP6: TestPoint; TestPoint_Pad_D1.0mm

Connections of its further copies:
+3V3: C34.2, C49.2, MOT2.8 (VCC_IO), MOT3.8 (VCC_IO), R39.1, R40.1, R57.1, R58.1; also elsewhere on the board
+6V: C68.2, C69.2, MOT2.30 (VSA), MOT3.30 (VSA); also elsewhere on the board
/CPU/AIN_REF: R43.1, R61.1; also elsewhere on the board
/CPU/CLK: R34.1, R52.1; also elsewhere on the board
/CPU/DRV1_DIAGNOSTIC: MOT2.21 (DIAG1_SWP), R40.2; also elsewhere on the board
/CPU/DRV1_DIR: R45.1; also elsewhere on the board
/CPU/DRV1_EN: R38.1; also elsewhere on the board
/CPU/DRV1_STEP: R44.1; also elsewhere on the board
/CPU/DRV2_DIAGNOSTIC: MOT3.21 (DIAG1_SWP), R58.2; also elsewhere on the board
/CPU/DRV2_DIR: R63.1; also elsewhere on the board
/CPU/DRV2_EN: R56.1; also elsewhere on the board
/CPU/DRV2_STEP: R62.1; also elsewhere on the board
/CPU/MISO: R32.1, R50.1; also elsewhere on the board
/CPU/MOSI: R33.1, R51.1; also elsewhere on the board
/CPU/~DRV1_SPI_SS: R35.1; also elsewhere on the board
/CPU/~DRV2_SPI_SS: R53.1; also elsewhere on the board
GND: C22.1, C23.1, C24.2, C25.2, C26.2, C27.2, C28.2, C29.2, C30.1, C31.1, C32.1, C33.1, C34.1, C37.1, C38.1, C39.2, C40.2, C41.2, C42.2, C43.2, C44.2, C45.1, C46.1, C47.1, C48.1, C49.1, C68.1, C69.1, C74.1, C75.1, J12.3, J13.3, MOT2.12 (GNDP_1), MOT2.24 (GNDA), MOT2.35 (GNDP_2), MOT2.36 (TST_MODE), MOT2.37 (GND_PAD), MOT3.12 (GNDP_1), MOT3.24 (GNDA), MOT3.35 (GNDP_2), MOT3.36 (TST_MODE), MOT3.37 (GND_PAD), R31.1, R36.1, R37.1, R41.1, R42.1, R46.1, R47.1, R49.1, R54.1, R55.1, R59.1, R60.1, R64.1, R65.1; also elsewhere on the board
unnamed: C26.1, J5.1, MOT2.34 (OA1)
unnamed: C27.1, J5.2, MOT2.32 (OA2)
unnamed: C28.1, J5.3, MOT2.13 (OB1)
unnamed: C29.1, J5.4, MOT2.15 (OB2)
unnamed: C41.1, J7.1, MOT3.34 (OA1)
unnamed: C42.1, J7.2, MOT3.32 (OA2)
unnamed: C43.1, J7.3, MOT3.13 (OB1)
unnamed: C44.1, J7.4, MOT3.15 (OB2)
unnamed: J12.1, MOT2.6 (STEP_REFL), R44.2
unnamed: J12.2, R78.1
unnamed: J13.1, MOT3.6 (STEP_REFL), R62.2
unnamed: J13.2, R79.1
unnamed: C32.2, MOT2.25 (5V_OUT), R48.2
unnamed: MOT2.23 (AIN_IREF), R43.2
unnamed: C31.2, MOT2.33 (BRA), R47.2, TP4.1
unnamed: C30.2, MOT2.14 (BRB), R46.2, TP3.1
unnamed: MOT2.1 (CLK), R31.2
unnamed: C20.1, MOT2.28 (CPI)
unnamed: C20.2, MOT2.27 (CPO)
unnamed: MOT2.18 (DCEN_ENCB_CFG4), R36.2
unnamed: MOT2.19 (DCIN_ENCA_CFG5), R37.2
unnamed: MOT2.17 (DCO_ENCN), R41.2
unnamed: MOT2.20 (DIAG0_SWN), R39.2
unnamed: MOT2.7 (DIR_REFR), R45.2
unnamed: MOT2.22 (DRV_~EN_CFG6), R38.2
unnamed: MOT2.3 (SCK_CFG2), R34.2
unnamed: MOT2.4 (SDI_CFG1), R33.2
unnamed: MOT2.5 (SDO_CFG0), R32.2
unnamed: MOT2.10 (SPI_MODE), R42.2
unnamed: C33.2, MOT2.26 (VCC), R48.1
unnamed: C21.1, MOT2.29 (VCP)
unnamed: MOT2.2 (~CS_CFG3), R35.2
unnamed: C47.2, MOT3.25 (5V_OUT), R66.2
unnamed: MOT3.23 (AIN_IREF), R61.2
unnamed: C46.2, MOT3.33 (BRA), R65.2, TP6.1
unnamed: C45.2, MOT3.14 (BRB), R64.2, TP5.1
unnamed: MOT3.1 (CLK), R49.2
unnamed: C35.1, MOT3.28 (CPI)
unnamed: C35.2, MOT3.27 (CPO)
unnamed: MOT3.18 (DCEN_ENCB_CFG4), R54.2
unnamed: MOT3.19 (DCIN_ENCA_CFG5), R55.2
unnamed: MOT3.17 (DCO_ENCN), R59.2
unnamed: MOT3.20 (DIAG0_SWN), R57.2
unnamed: MOT3.7 (DIR_REFR), R63.2
unnamed: MOT3.22 (DRV_~EN_CFG6), R56.2
unnamed: MOT3.3 (SCK_CFG2), R52.2
unnamed: MOT3.4 (SDI_CFG1), R51.2
unnamed: MOT3.5 (SDO_CFG0), R50.2
unnamed: MOT3.10 (SPI_MODE), R60.2
unnamed: C48.2, MOT3.26 (VCC), R66.1
unnamed: C36.1, MOT3.29 (VCP)
unnamed: MOT3.2 (~CS_CFG3), R53.2
VEXT: C21.2, C22.2, C23.2, C24.1, C25.1, C36.2, C37.2, C38.2, C39.1, C40.1, C74.2, C75.2, MOT2.16 (VS_1), MOT2.31 (VS_2), MOT3.16 (VS_1), MOT3.31 (VS_2), R78.2, R79.2; also elsewhere on the board

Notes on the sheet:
TMC2130-CONFIGURATION
DEBUG STEP SIGNAL SERVO MOTOR OPTIONS (SG90 - SAVOX)
SPI_MODE - PIN 10 - HIGH(internal pull up) - SPI interface selected
DCEN_CFG4 - PIN 18 - LOW - no DcStep

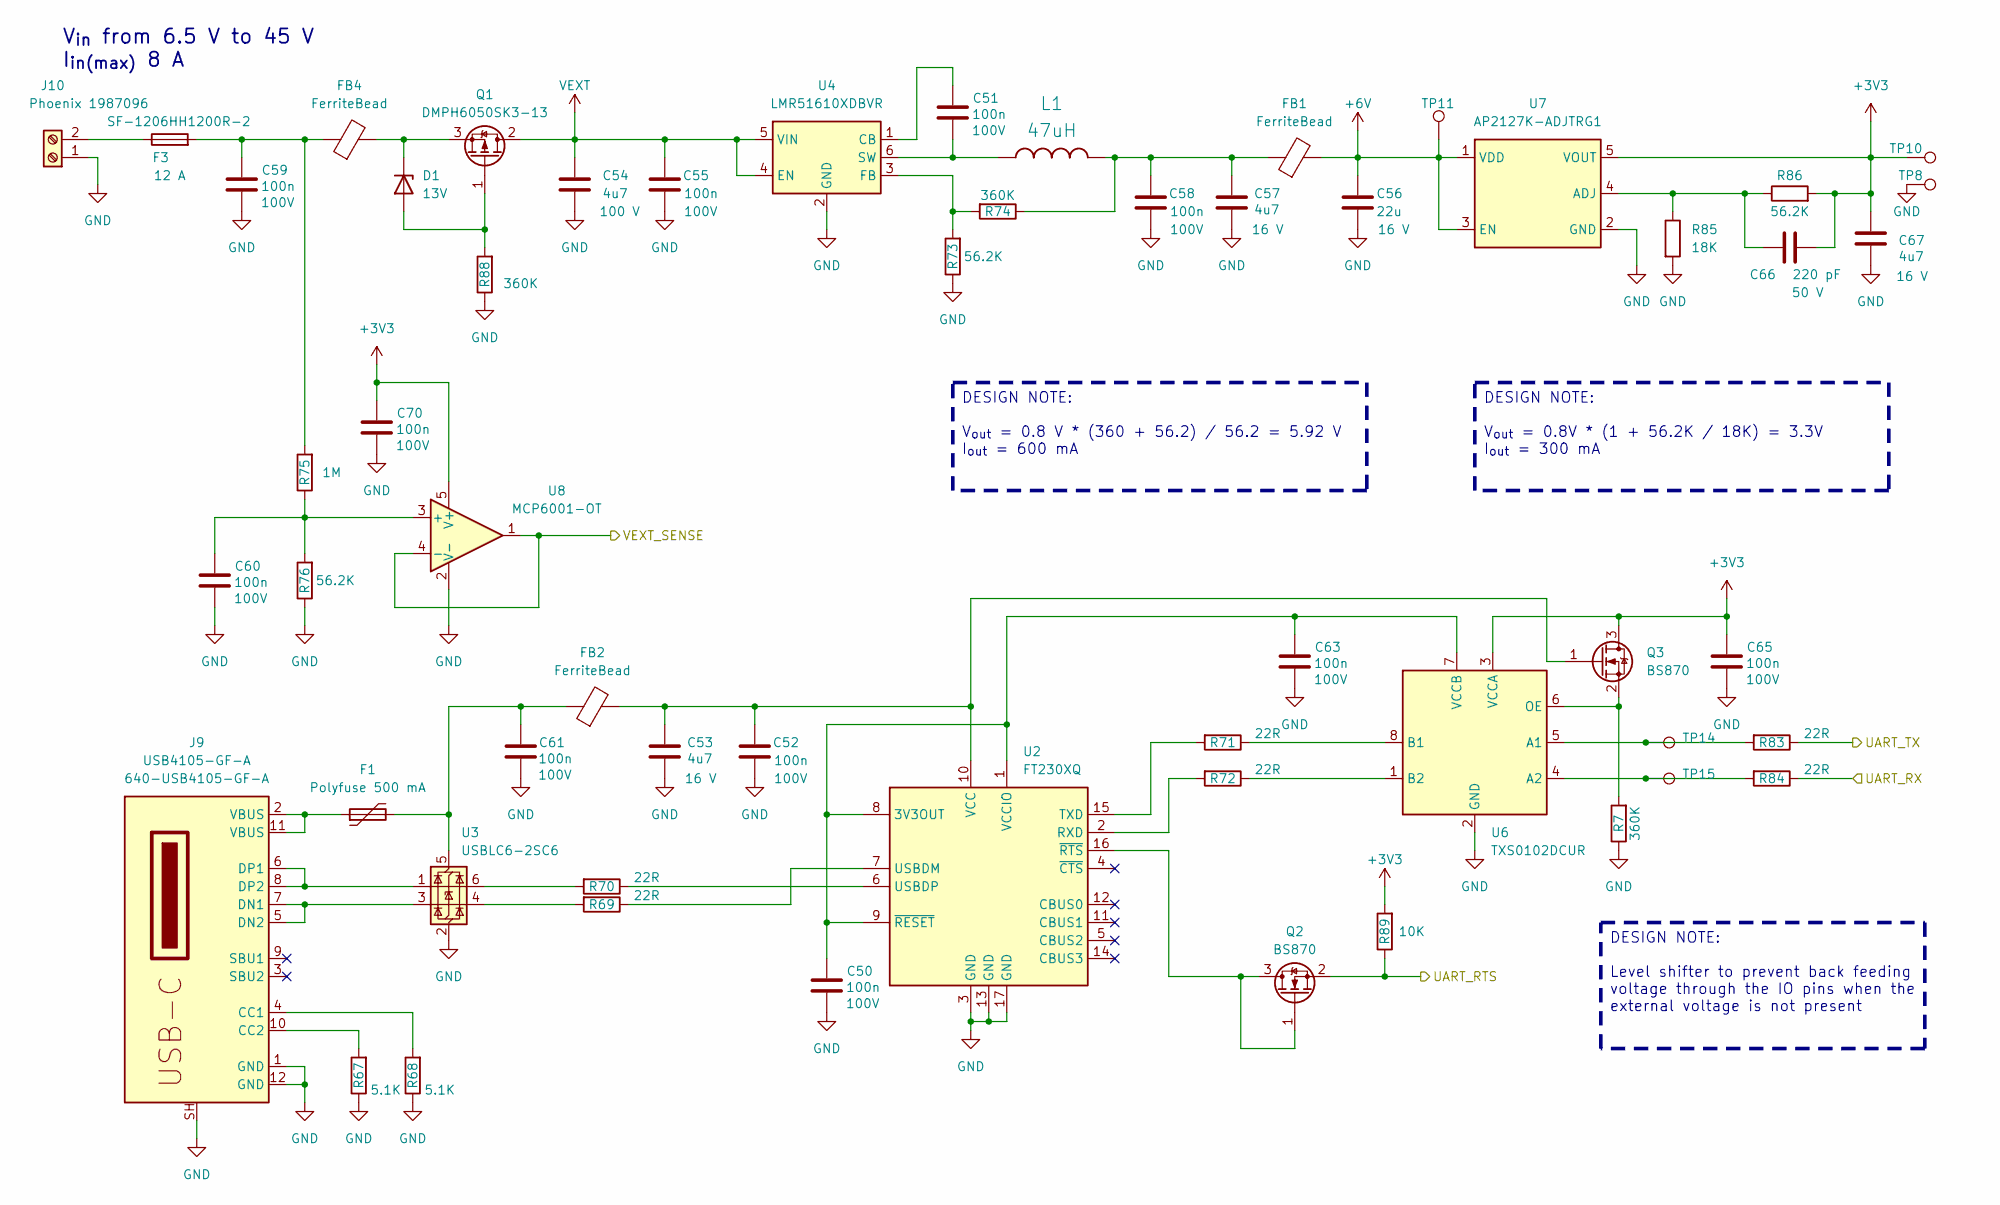
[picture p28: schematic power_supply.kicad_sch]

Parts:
C50, C51, C52, C55, C58, C59, C60, C61, C63, C65, C70: 100n; C_0603_1608Metric_Pad1.08x0.95mm_HandSolder; Voltage 100V; Mouser 187-CL10B104KC8NNNC
C53, C57, C67: 4u7; C_0805_2012Metric_Pad1.18x1.45mm_HandSolder; Voltage 16 V; Mouser 81-GRM21BR71C475KE1L
C54: 4u7; C_1206_3216Metric_Pad1.33x1.80mm_HandSolder; Voltage 100 V; Mouser 81-GRM31CZ72A475K11L
C56: 22u; C_1206_3216Metric_Pad1.33x1.80mm_HandSolder; Voltage 16 V; Mouser 187-CL31A226MOCLNNC
C66: 220 pF; C_0603_1608Metric_Pad1.08x0.95mm_HandSolder; Voltage 50 V; Mouser 80-C0603C221J5GAUTLR
D1: 13V; D_SOD-123; Mouser 771-BZT52-C13J
F1: Polyfuse 500 mA; Fuse_1210_3225Metric_Pad1.42x2.65mm_HandSolder; Mouser 650-MICROSMD050F-2
F3: 12 A; Fuse_1206_3216Metric_Pad1.42x1.75mm_HandSolder; Mouser SF-1206HH1200R-2
FB1, FB2, FB4: FerriteBead; Wurth_CBF_0805; Mouser 710-742792030
J9: USB4105-GF-A; USB-TYPE-C-12P; Mouser 640-USB4105-GF-A
J10: Phoenix 1987096; TerminalBlock_Phoenix_MKDS-1,5-2-5.08_1x02_P5.08mm_Horizont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; Mouser 651-1987096
L1: 47uH; L_Taiyo-Yuden_NR-60xx; Mouser 963-NRS6028T470MMGJ
Q1: DMPH6050SK3-13; TO-252-2; Mouser 621-DMPH6050SK3-13
Q2, Q3: BS870; SOT-23; Mouser 621-BS870-F
R7, R74, R88: 360K; R_0603_1608Metric_Pad0.98x0.95mm_HandSolder; Mouser 603-RT0603FRE07360KL
R67, R68: 5.1K; R_0603_1608Metric_Pad0.98x0.95mm_HandSolder; Mouser 603-RC0603FR-105K1L
R69, R70, R71, R72, R83, R84: 22R; R_0603_1608Metric_Pad0.98x0.95mm_HandSolder; Mouser 603-AC0603JR-0722RL
R73, R76, R86: 56.2K; R_0603_1608Metric_Pad0.98x0.95mm_HandSolder; Mouser 603-RC0402FR-0756K2L
R75: 1M; R_0603_1608Metric_Pad0.98x0.95mm_HandSolder; Mouser 603-RC0603FR-071ML
R85: 18K; R_0603_1608Metric_Pad0.98x0.95mm_HandSolder; Mouser 603-RC0402FR-0718KL
R89: 10K; R_0603_1608Metric_Pad0.98x0.95mm_HandSolder; Mouser 603-RC0603JR-0710KL
TP8, TP10, TP11, TP14, TP15: TestPoint_Pad_D1.0mm
U2: FT230XQ; QFN-16-1EP_4x4mm_P0.65mm_EP2.1x2.1mm; Mouser 895-FT230XQ-R
U3: USBLC6-2SC6; SOT-23-6; Mouser 511-USBLC6-2SC6
U4: LMR51610XDBVR; SOT-23-6; Mouser 595-LMR51610XDBVR
U6: TXS0102DCUR; VSSOP-8_2.3x2mm_P0.5mm; MPN TXS0102DCUR; LCSC C53434
U7: AP2127K-ADJTRG1; SOT-23-5; MPN AP2127K-ADJTRG1; LCSC C96343
U8: MCP6001-OT; SOT-23-5; Mouser 579-MCP6001T-E/OT

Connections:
+3V3: C65.1, C66.2, C67.2, C70.1, Q3.3 (D), R86.2, R89.2, TP10.1, U6.3 (VCCA), U7.5 (VOUT), U8.5 (V+); also elsewhere on the board
+6V: C56.2, FB1.2, TP11.1, U7.1 (VDD), U7.3 (EN); also elsewhere on the board
/CPU/MOD_NWAKE: Q2.2 (S), R89.1; also elsewhere on the board
/CPU/MOD_RX: R83.1; also elsewhere on the board
/CPU/MOD_TX: R84.1; also elsewhere on the board
/CPU/VEXT_SENSE: U8.1, U8.4 (-); also elsewhere on the board
GND: C50.2, C52.2, C53.1, C54.1, C55.2, C56.1, C57.1, C58.2, C59.2, C60.2, C61.2, C63.2, C65.2, C67.1, C70.2, J9.1 (GND), J9.12 (GND), J9.SH (SHIELD), J10.1, R7.1, R67.1, R68.1, R73.1, R76.1, R85.2, R88.1, TP8.1, U2.3 (GND), U2.13 (GND), U2.17 (GND), U3.2 (GND), U4.2 (GND), U6.2 (GND), U7.2 (GND), U8.2 (V-); also elsewhere on the board
unnamed: C57.2, C58.1, FB1.1, L1.2, R74.1
unnamed: C59.1, F3.2, FB4.1, R75.2
unnamed: D1.2 (A), Q1.1 (G), R88.2
unnamed: D1.1 (K), FB4.2, Q1.3 (S)
unnamed: F1.1, J9.2 (VBUS), J9.11 (VBUS)
unnamed: J9.4 (CC1), R68.2
unnamed: J9.10 (CC2), R67.2
unnamed: J9.5 (DN2), J9.7 (DN1), U3.3 (I/O2)
unnamed: J9.6 (DP1), J9.8 (DP2), U3.1 (I/O1)
unnamed: F3.1, J10.2
unnamed: Q2.1 (G), Q2.3 (D), U2.16 (~RTS)
unnamed: C52.1, C53.2, FB2.2, Q3.1 (G), U2.10 (VCC)
unnamed: Q3.2 (S), R7.2, U6.6 (OE)
unnamed: R69.2, U3.4 (I/O2)
unnamed: R70.2, U3.6 (I/O1)
unnamed: C50.1, C63.1, U2.1 (VCCIO), U2.8 (3V3OUT), U2.9 (~RESET), U6.7 (VCCB)
unnamed: R72.2, U2.2 (RXD)
unnamed: R71.2, U2.15 (TXD)
unnamed: R69.1, U2.7 (USBDM)
unnamed: R70.1, U2.6 (USBDP)
unnamed: C61.1, F1.2, FB2.1, U3.5 (VBUS)
unnamed: C51.1, U4.1 (CB)
unnamed: R73.2, R74.2, U4.3 (FB)
unnamed: C51.2, L1.1, U4.6 (SW)
unnamed: R83.2, TP14.1, U6.5 (A1)
unnamed: R84.2, TP15.1, U6.4 (A2)
unnamed: R71.1, U6.8 (B1)
unnamed: R72.1, U6.1 (B2)
unnamed: C66.1, R85.1, R86.1, U7.4 (ADJ)
unnamed: C60.1, R75.1, R76.2, U8.3 (+)
VEXT: C54.2, C55.1, Q1.2 (D), U4.4 (EN), U4.5 (VIN); also elsewhere on the board

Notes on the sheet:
DESIGN NOTE: Level shifter to prevent back feeding voltage through the IO pins when the external voltage is not present
DESIGN NOTE: V_{out} = 0.8 V * (360 + 56.2) / 56.2 = 5.92 V I_{out} = 600 mA
DESIGN NOTE: V_{out} = 0.8V * (1 + 56.2K / 18K) = 3.3V I_{out} = 300 mA
V_{in} from 6.5 V to 45 V I_{in(max)} 8 A

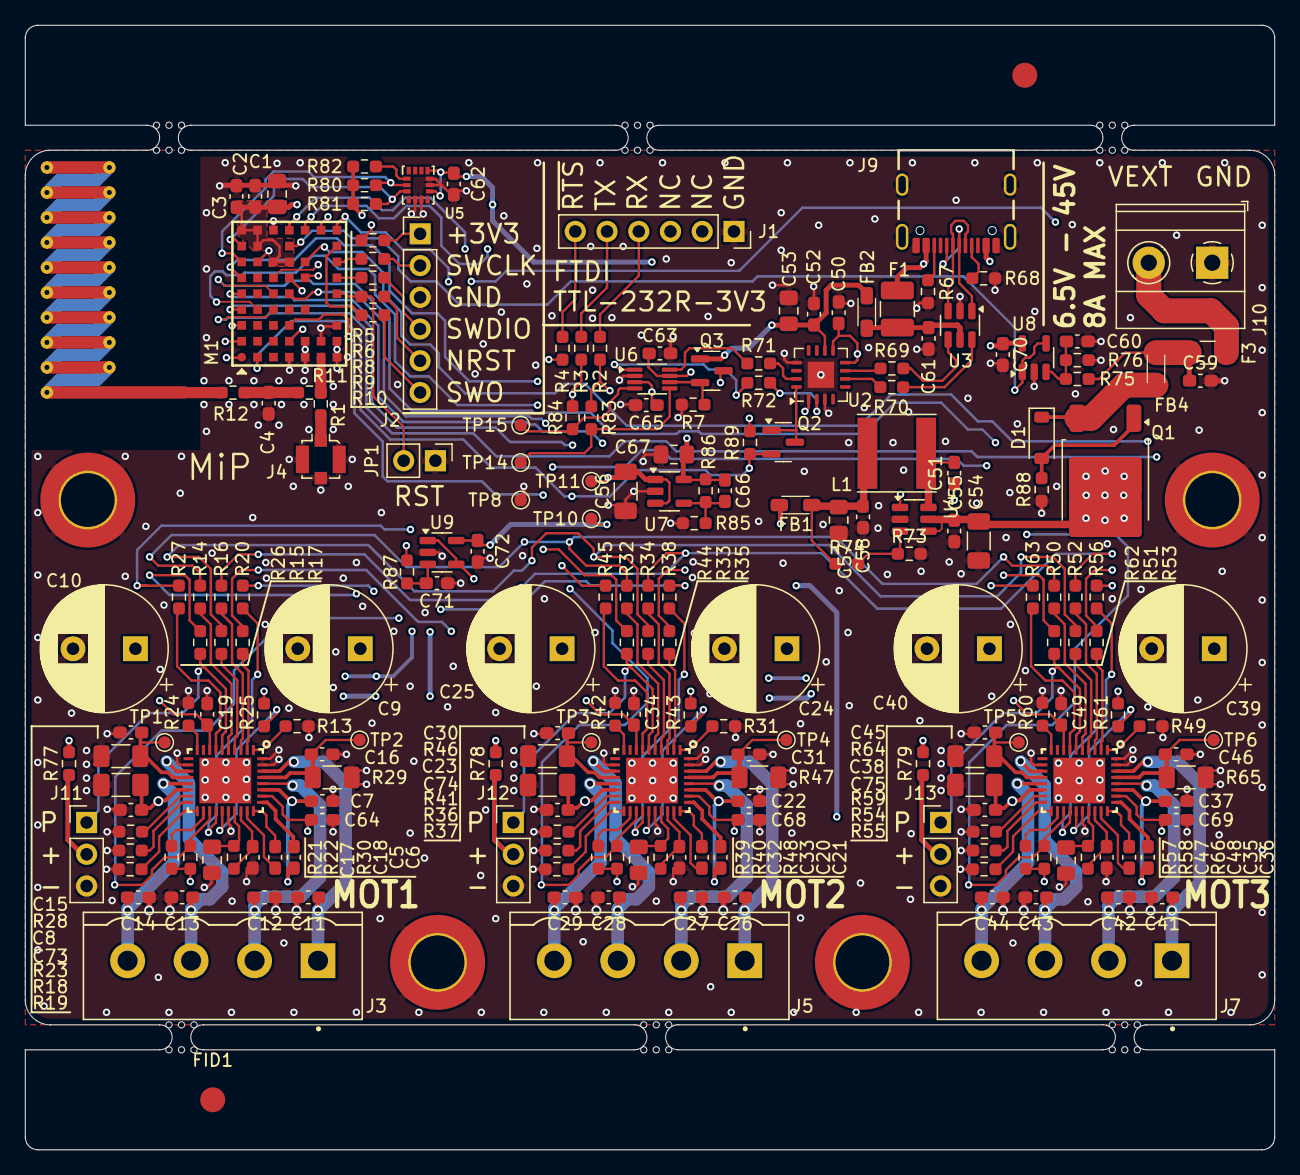
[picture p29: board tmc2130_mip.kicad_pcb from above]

Board: 4 copper layers, 100.0 x 90.0 mm, 219 parts (0 on the bottom side), 156 nets.

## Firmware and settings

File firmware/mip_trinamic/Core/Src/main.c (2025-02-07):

/*******************************************************************************
 * Included files
 *****************************************************************************/
#include "FreeRTOS.h"
#include "task.h"
#include "main.h"
#include "trinamic_spi.h"
#include "trinamic_gpio.h"
#include "trinamic_pulse_gen.h"
#include "trinamic_uart.h"
#include "trinamic_tim.h"
#include "trinamic_iic.h"
#include "trinamic_conf.h"
#include "trinamic_dac.h"
#include "app_diagnosis.h"
#include "app_cli.h"
#include "ipcc.h"
#include "app_cortexcomm.h"
#include "app_mipd.h"

/*******************************************************************************
 * Definitions
 ******************************************************************************/

/*******************************************************************************
 * Prototypes
 ******************************************************************************/
static void SystemClock_Config(void);

/*******************************************************************************
 * Variables
 ******************************************************************************/

/*******************************************************************************
 * Code
 ******************************************************************************/
void vApplicationIdleHook(void)
{
	/* User adds here LOW POWER features */
	;
}

int main(void)
{
	/* Low Level clock configuration */
	(void)HAL_Init();
	(void)SystemClock_Config();

	/* GPIO and peripherals */
	(void)IPCC_Init();
	(void)TrinamicGPIO_Init();
	(void)TIM2_Init();
	(void)TIM16_Init();
	//(void)LPUART_Init();
	(void)SPI2_Init();
	(void)I2C1_Init();
	(void)DAC_Init();

	/* Set default state from potential system reset: Clear Stop2 flag of CPU1 */
	__HAL_PWR_CLEAR_FLAG(PWR_FLAG_STOP2);

	/* System configuration */
	(void)TrinamicInit();

	/* Boot CPU2 */
	(void)HAL_PWREx_ReleaseCore(PWR_CORE_CPU2);

	/* Wait until cpu2 is ready to receive commands */
	while (*cpu2InitDone != CPU2_INITIALISED)
	{
		__asm("NOP");
	}

	/* Starting Tasks */
	//(void)vTaskStepperDiagnosis();
	(void)vTaskCli();
	(void)MipdTask();

	/* Enable FreeRTOS */
	(void)vTaskStartScheduler();
	for(;;);
}

static void SystemClock_Config(void)
{
	RCC_OscInitTypeDef RCC_OscInitStruct = {0};
	RCC_ClkInitTypeDef RCC_ClkInitStruct = {0};
	RCC_PeriphCLKInitTypeDef PeriphClkInit = {0};

	/* Configure the main internal regulator output voltage */
	__HAL_PWR_VOLTAGESCALING_CONFIG(PWR_REGULATOR_VOLTAGE_SCALE1);

	/* MSI is enabled after System reset, activate PLL with MSI as source */
	RCC_OscInitStruct.OscillatorType =  RCC_OSCILLATORTYPE_LSE | RCC_OSCILLATORTYPE_MSI |
									  RCC_OSCILLATORTYPE_HSE |RCC_OSCILLATORTYPE_HSI;
	RCC_OscInitStruct.HSEState = RCC_HSE_BYPASS_PWR;
	RCC_OscInitStruct.HSEDiv = RCC_HSE_DIV1;
	RCC_OscInitStruct.LSEState = RCC_LSE_ON;
	RCC_OscInitStruct.MSIState = RCC_MSI_ON;
	RCC_OscInitStruct.HSIState = RCC_HSI_ON;
	RCC_OscInitStruct.HSICalibrationValue = RCC_HSICALIBRATION_DEFAULT;
	RCC_OscInitStruct.MSICalibrationValue = RCC_MSICALIBRATION_DEFAULT;
	RCC_OscInitStruct.MSIClockRange = RCC_MSIRANGE_11; /*System Clock set at 48 MHz*/

	/*Activate PLL, HSE clock source, System Clock 48 MHz*/
	RCC_OscInitStruct.PLL.PLLState = RCC_PLL_ON;
	RCC_OscInitStruct.PLL.PLLSource = RCC_PLLSOURCE_HSE;
	RCC_OscInitStruct.PLL.PLLM = RCC_PLLM_DIV4;
	RCC_OscInitStruct.PLL.PLLN = 12;
	RCC_OscInitStruct.PLL.PLLR = RCC_PLLR_DIV2;
	RCC_OscInitStruct.PLL.PLLQ = RCC_PLLQ_DIV2;
	RCC_OscInitStruct.PLL.PLLP = RCC_PLLP_DIV2;
	HAL_RCC_OscConfig(&RCC_OscInitStruct);
	CLEAR_BIT(SysTick->CTRL,SysTick_CTRL_TICKINT_Msk);
	CLEAR_BIT(SysTick->CTRL,SysTick_CTRL_ENABLE_Msk);

	/**Initializes the CPU, AHB and APB busses clocks*/

	RCC_ClkInitStruct.ClockType = (RCC_CLOCKTYPE_SYSCLK | RCC_CLOCKTYPE_HCLK |
								 RCC_CLOCKTYPE_HCLK2 | RCC_CLOCKTYPE_PCLK1 |
								 RCC_CLOCKTYPE_PCLK2 | RCC_CLOCKTYPE_HCLK3);
	RCC_ClkInitStruct.SYSCLKSource   = RCC_SYSCLKSOURCE_PLLCLK;
	RCC_ClkInitStruct.AHBCLKDivider  = RCC_SYSCLK_DIV1;
	RCC_ClkInitStruct.AHBCLK2Divider = RCC_SYSCLK_DIV1;
	RCC_ClkInitStruct.APB1CLKDivider = RCC_HCLK_DIV1;
	RCC_ClkInitStruct.APB2CLKDivider = RCC_HCLK_DIV1;
	RCC_ClkInitStruct.AHBCLK3Divider = RCC_SYSCLK_DIV1;
	HAL_RCC_ClockConfig(&RCC_ClkInitStruct, FLASH_LATENCY_2);
	CLEAR_BIT(SysTick->CTRL,SysTick_CTRL_TICKINT_Msk);
	CLEAR_BIT(SysTick->CTRL,SysTick_CTRL_ENABLE_Msk);

	PeriphClkInit.PeriphClockSelection = RCC_PERIPHCLK_RTC;
	PeriphClkInit.RTCClockSelection = RCC_RTCCLKSOURCE_LSE;
	HAL_RCCEx_PeriphCLKConfig(&PeriphClkInit);
	CLEAR_BIT(SysTick->CTRL,SysTick_CTRL_TICKINT_Msk);
	CLEAR_BIT(SysTick->CTRL,SysTick_CTRL_ENABLE_Msk);
}

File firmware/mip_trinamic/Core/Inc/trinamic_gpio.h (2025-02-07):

#ifndef CORE_INC_TRINAMIC_GPIO_H_
#define CORE_INC_TRINAMIC_GPIO_H_

/*******************************************************************************
 * Included files
 *****************************************************************************/
#include "main.h"

/*******************************************************************************
 * Definitions
 ******************************************************************************/

#define TRINAMIC_MOT0_ID 0
#define TRINAMIC_MOT1_ID 1
#define TRINAMIC_MOT2_ID 2

/* MOT 0 */
#define DRV0_STEP_Pin			GPIO_PIN_10
#define DRV0_STEP_Port 			GPIOB

#define DRV0_DIR_Pin			GPIO_PIN_6
#define DRV0_DIR_Port  			GPIOA

#define DRV0_EN_Pin				GPIO_PIN_5
#define DRV0_EN_Port  			GPIOA

#define DRV0_DIAGNOSTIC_Pin		GPIO_PIN_2
#define DRV0_DIAGNOSTIC_Port  	GPIOB

#define DRV0_SPI_NSS_Pin		GPIO_PIN_4
#define DRV0_SPI_NSS_Port  		GPIOA

/* MOT 1 */
#define DRV1_STEP_Pin			GPIO_PIN_11
#define DRV1_STEP_Port 			GPIOB

#define DRV1_DIR_Pin			GPIO_PIN_14
#define DRV1_DIR_Port  			GPIOB

#define DRV1_EN_Pin		        GPIO_PIN_4
#define DRV1_EN_Port	        GPIOB

#define DRV1_DIAGNOSTIC_Pin		GPIO_PIN_3
#define DRV1_DIAGNOSTIC_Port	GPIOA

#define DRV1_SPI_NSS_Pin		GPIO_PIN_12
#define DRV1_SPI_NSS_Port  		GPIOB

/* MOT 2 */
#define DRV2_EN_Pin		        GPIO_PIN_1
#define DRV2_EN_Port	        GPIOA

#define DRV2_STEP_Pin		    GPIO_PIN_0
#define DRV2_STEP_Port	        GPIOA

#define DRV2_DIR_Pin			GPIO_PIN_5
#define DRV2_DIR_Port 			GPIOB

#define DRV2_DIAGNOSTIC_Pin		GPIO_PIN_15
#define DRV2_DIAGNOSTIC_Port	GPIOA

#define DRV2_SPI_NSS_Pin		GPIO_PIN_12
#define DRV2_SPI_NSS_Port  		GPIOA

/* SPI */
#define SPI2_MOSI_Pin			GPIO_PIN_3
#define SPI2_MOSI_Port  		GPIOC

#define SPI2_MISO_Pin			GPIO_PIN_2
#define SPI2_MISO_Port  		GPIOC

#define SPI2_CLK_Pin			GPIO_PIN_9
#define SPI2_CLK_Port  		    GPIOA

/* FTDI */
#define MOD_TX_Pin				GPIO_PIN_0
#define MOD_TX_Port				GPIOC

#define MOD_RX_Pin				GPIO_PIN_1
#define MOD_RX_Port				GPIOC

#define MOD_NWAKE_Pin			GPIO_PIN_7
#define MOD_NWAKE_Port			GPIOA

/* IIC */
#define IIC_SCL_Pin				GPIO_PIN_8
#define IIC_SCL_Port			GPIOB

#define IIC_SDA_Pin				GPIO_PIN_9
#define IIC_SDA_Port			GPIOB

/* GPIO DEBUG */
#define GPIO0_NWAKE_Pin			GPIO_PIN_7
#define GPIO0_NWAKE_Port		GPIOA

/* BATTERY MEASUREMENT & DAC */
#define AIN_IREF_MIP_Pin		GPIO_PIN_10
#define AIN_IREF_MIP_Port  		GPIOA

#define VEXT_SENSE_Pin			GPIO_PIN_13
#define VEXT_SENSE_Port  		GPIOB

/*******************************************************************************
* API
******************************************************************************/
void TrinamicGPIO_Init(void);
void TrinamicNSS_Select(uint8_t driver);
void TrinamicNSS_Idle(void);
void TrinamicMotXEnable(uint8_t driver);
void TrinamicMotXDisable(uint8_t driver);

#endif

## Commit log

2025-01-07 added pcbway format bom, added pcb production document
    [BOM_PCBWay.xlsx]
2025-01-08 added sch images
    [BOM_PCBWay.xlsx]
2025-01-08 added firmware schematic implementation img
2025-01-10 fixed bom, cortex m0 wakeup ok
    [BOM_PCBWay.xlsx]
2025-01-10 added LoRa module Driver, Module demo app running
2025-01-17 fixed layout error on u4
    [power_supply.kicad_sch, tmc2130_mip.kicad_pcb, tmc2130_mip.kicad_sch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]
2025-01-17 spi ok, all 3 drivers completed init procedure, first steps with stepper
2025-01-17 added new images, linked to PCBWay
2025-02-06 output 2.5 from dac pin to trinamic drivers
2025-02-07 board transmits correctly radio frames
    [ipcc.c, main.c, mip_a.c]
